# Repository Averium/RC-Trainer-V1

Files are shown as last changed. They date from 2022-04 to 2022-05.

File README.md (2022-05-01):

# RC-Trainer-V1

This project is a legal sized trainer RC aircraft design

# Specifications:

- Mass:         182 g
- Length:       520 mm
- Wingspawn:    708 mm
- CG:           157 mm

- Powerplant:   1 x 600 mah LIPO  -  1 x EMAX MT1806 2280 kv  -  5030 propeller (2 blade)
        
- 4 Channels:   Throttle - Elevator - Rudder - Ailerons

# Materials:
  - 5 mm foam board sheet
  - 3 mm plywood sheet
  - 4 mm BBQ stick
  - 12 x 12 mm balsa slat
  - 1 mm spring steel wire
  - 3D printed PLA plastic

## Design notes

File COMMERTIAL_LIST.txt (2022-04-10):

Motor		EMAX MT1806 2280kv
ESC		BHeli 12A		
Servo		3.7g micro
Propeller	5030 CF
Receiver	FS2A-4CH
Battery 	2s lipo 600 mah

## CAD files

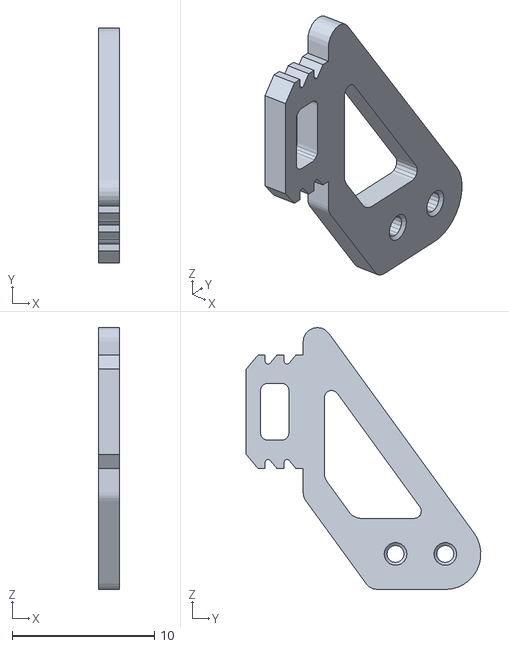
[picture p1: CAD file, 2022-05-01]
PARTS/PP-00-0-CONTROL_HORN/PP-00-0-0-M1.stl
1.50 x 16.5 x 18.4

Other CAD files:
PARTS/PP-00-0-CONTROL_HORN/PP-00-0-0-M2.stl
ASSEMBLY/A-00-0-MAIN/A-00-0.iam
ASSEMBLY/A-00-0-MAIN/A-00-0.idw
ASSEMBLY/A-01-0-FUSELAGE/A-01-0.iam
ASSEMBLY/A-01-0-FUSELAGE/A-01-0.idw
ASSEMBLY/A-01-0-FUSELAGE/A-01-0.ipn
ASSEMBLY/A-02-0-WING/A-02-0.iam
ASSEMBLY/A-02-0-WING/A-02-0.idw
ASSEMBLY/A-02-0-WING/A-02-0.ipn
ASSEMBLY/A-03-0-ONE_LEVEL/A-03-0.iam
PARTS/C-00-0-BATTERY_600MAH/C-00-0.ipt
PARTS/C-01-0-EMAX_MT1806_2280KV/C-01-0.ipt
PARTS/C-02-0-EMAX_12AESC/C-02-0.ipt
PARTS/C-03-0-SERVO_3G/C-03-0.ipt
PARTS/C-03-0-SERVO_3G/C-03-0/CCW.ipt
PARTS/C-03-0-SERVO_3G/C-03-0/CW.ipt
PARTS/C-04-0-SERVO_LINKAGE_STOPPER/C-04-0.ipt
PARTS/C-05-0-FS2A_4CH/C-05-0.ipt
PARTS/C-06-0-5030_PROPELLER/C-06-0.ipt
PARTS/PF-00-0-WING/PF-00-0-0.idw
PARTS/PF-00-0-WING/PF-00-0-0.ipt
PARTS/PF-00-0-WING/PF-00-0-1.ipt
PARTS/PF-01-0-FUSELAGE/PF-01-0-0.idw
PARTS/PF-01-0-FUSELAGE/PF-01-0-0.ipt
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

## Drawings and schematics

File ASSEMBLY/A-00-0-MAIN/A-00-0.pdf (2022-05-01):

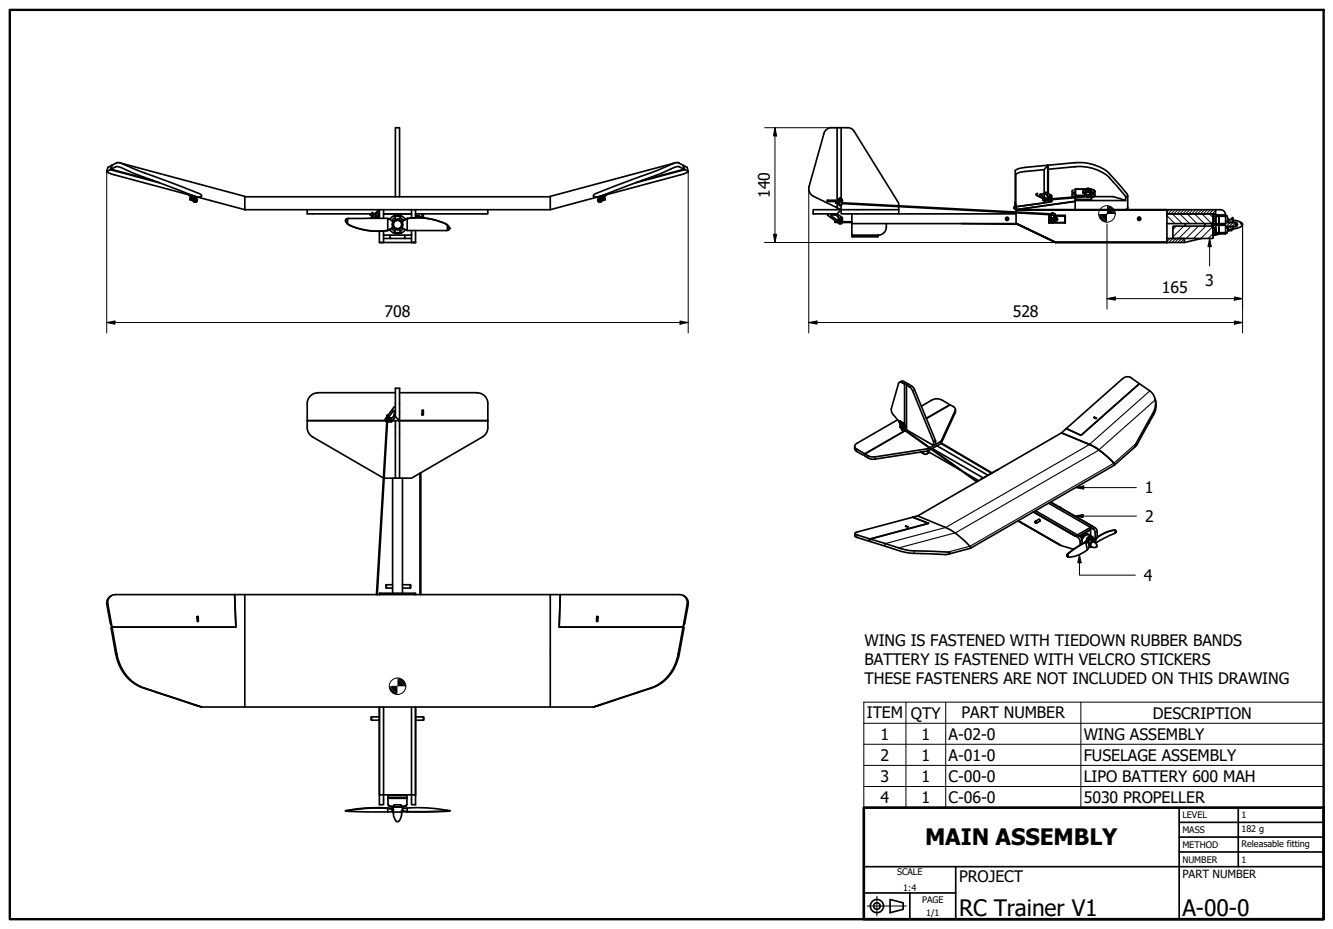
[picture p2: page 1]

WING IS FASTENED WITH TIEDOWN RUBBER BANDS
BATTERY IS FASTENED WITH VELCRO STICKERS
THESE FASTENERS ARE NOT INCLUDED ON THIS DRAWING

ITEM | QTY | PART NUMBER | DESCRIPTION
1 | 1 | A-02-0 | WING ASSEMBLY
2 | 1 | A-01-0 | FUSELAGE ASSEMBLY
3 | 1 | C-00-0 | LIPO BATTERY 600 MAH
4 | 1 | C-06-0 | 5030 PROPELLER
MAIN ASSEMBLY | LEVEL | 1

MASS | 182 g
METHOD | Releasable fitting
NUMBER | 1

SCALE 1:4 | PROJECT RC Trainer V1 | PART NUMBER A-00-0

PAGE 1/1

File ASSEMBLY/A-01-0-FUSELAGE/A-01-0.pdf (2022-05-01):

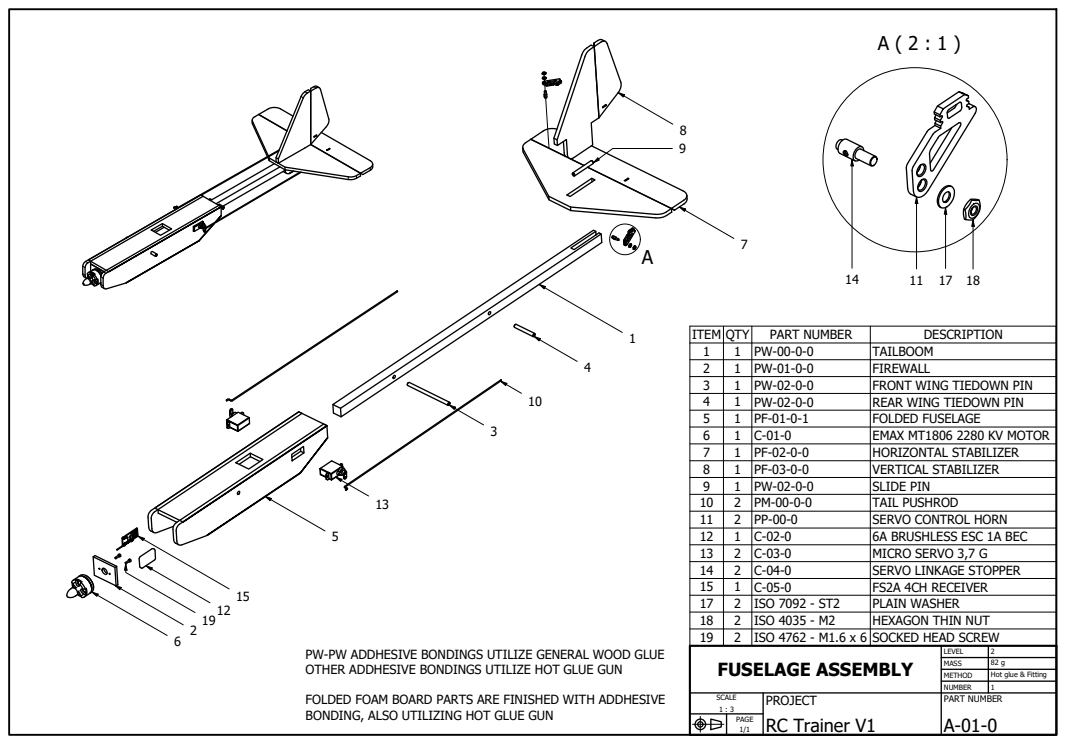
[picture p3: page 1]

ITEM | QTY | PART NUMBER | DESCRIPTION
1 | 1 | PW-00-0-0 | TAILBOOM
2 | 1 | PW-01-0-0 | FIREWALL
3 | 1 | PW-02-0-0 | FRONT WING TIEDOWN PIN
4 | 1 | PW-02-0-0 | REAR WING TIEDOWN PIN
5 | 1 | PF-01-0-1 | FOLDED FUSELAGE
6 | 1 | C-01-0 | EMAX MT1806 2280 KV MOTOR
7 | 1 | PF-02-0-0 | HORIZONTAL STABILIZER
8 | 1 | PF-03-0-0 | VERTICAL STABILIZER
9 | 1 | PW-02-0-0 | SLIDE PIN
10 | 2 | PM-00-0-0 | TAIL PUSHROD
11 | 2 | PP-00-0 | SERVO CONTROL HORN
12 | 1 | C-02-0 | 6A BRUSHLESS ESC 1A BEC
13 | 2 | C-03-0 | MICRO SERVO 3,7 G
14 | 2 | C-04-0 | SERVO LINKAGE STOPPER
15 | 1 | C-05-0 | FS2A 4CH RECEIVER
17 | 2 | ISO 7092 - ST2 | PLAIN WASHER
18 | 2 | ISO 4035 - M2 | HEXAGON THIN NUT
19 | 2 | ISO 4762 - M1.6 x 6 | SOCKED HEAD SCREW
FUSELAGE ASSEMBLY | LEVEL | 2

PW-PW ADDHESIVE BONDINGS UTILIZE GENERAL WOOD GLUE
OTHER ADDHESIVE BONDINGS UTILIZE HOT GLUE GUN

MASS | 82 g
METHOD | Hot glue & Fitting
NUMBER | 1

FOLDED FOAM BOARD PARTS ARE FINISHED WITH ADDHESIVE
BONDING, ALSO UTILIZING HOT GLUE GUN

SCALE 1 : 3 | PROJECT RC Trainer V1 | PART NUMBER A-01-0

PAGE 1/1

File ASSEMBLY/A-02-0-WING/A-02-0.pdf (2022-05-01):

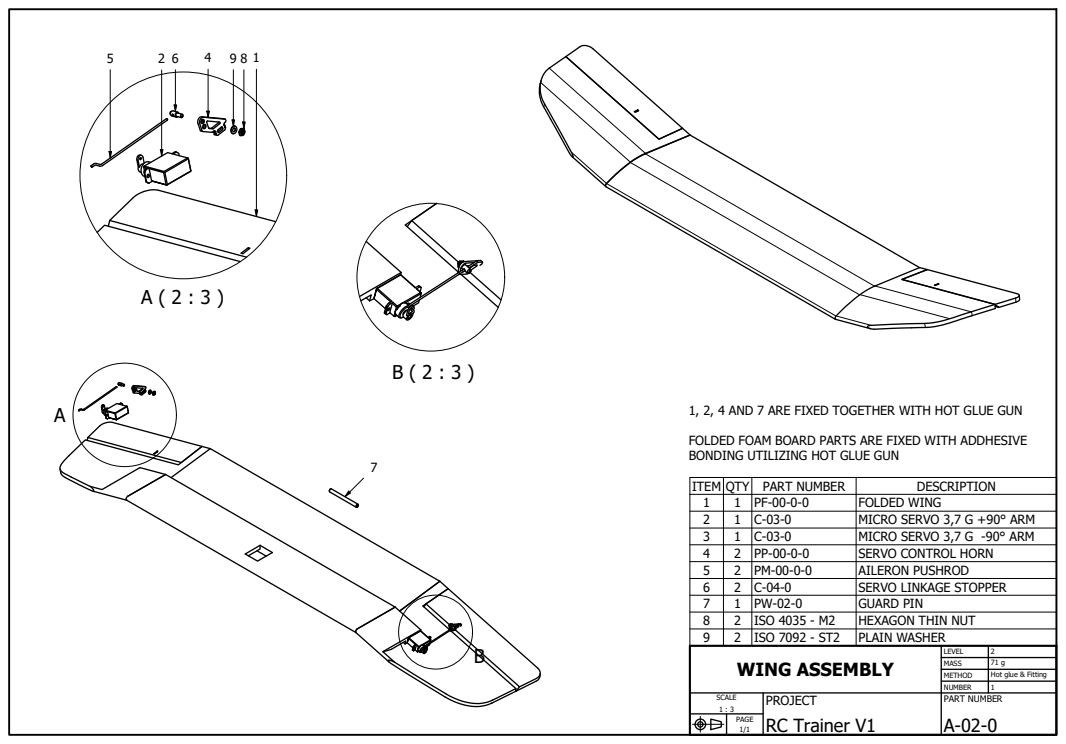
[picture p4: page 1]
WING ASSEMBLY

1, 2, 4 AND 7 ARE FIXED TOGETHER WITH HOT GLUE GUN

FOLDED FOAM BOARD PARTS ARE FIXED WITH ADDHESIVE
BONDING UTILIZING HOT GLUE GUN

ITEM | QTY | PART NUMBER | DESCRIPTION
1 | 1 | PF-00-0-0 | FOLDED WING
2 | 1 | C-03-0 | MICRO SERVO 3,7 G +90° ARM
3 | 1 | C-03-0 | MICRO SERVO 3,7 G -90° ARM
4 | 2 | PP-00-0-0 | SERVO CONTROL HORN
5 | 2 | PM-00-0-0 | AILERON PUSHROD
6 | 2 | C-04-0 | SERVO LINKAGE STOPPER
7 | 1 | PW-02-0 | GUARD PIN
8 | 2 | ISO 4035 - M2 | HEXAGON THIN NUT
9 | 2 | ISO 7092 - ST2 | PLAIN WASHER

LEVEL | 2
MASS | 71 g
METHOD | Hot glue & Fitting
NUMBER | 1

SCALE 1 : 3 | PROJECT RC Trainer V1 | PART NUMBER A-02-0

PAGE 1/1

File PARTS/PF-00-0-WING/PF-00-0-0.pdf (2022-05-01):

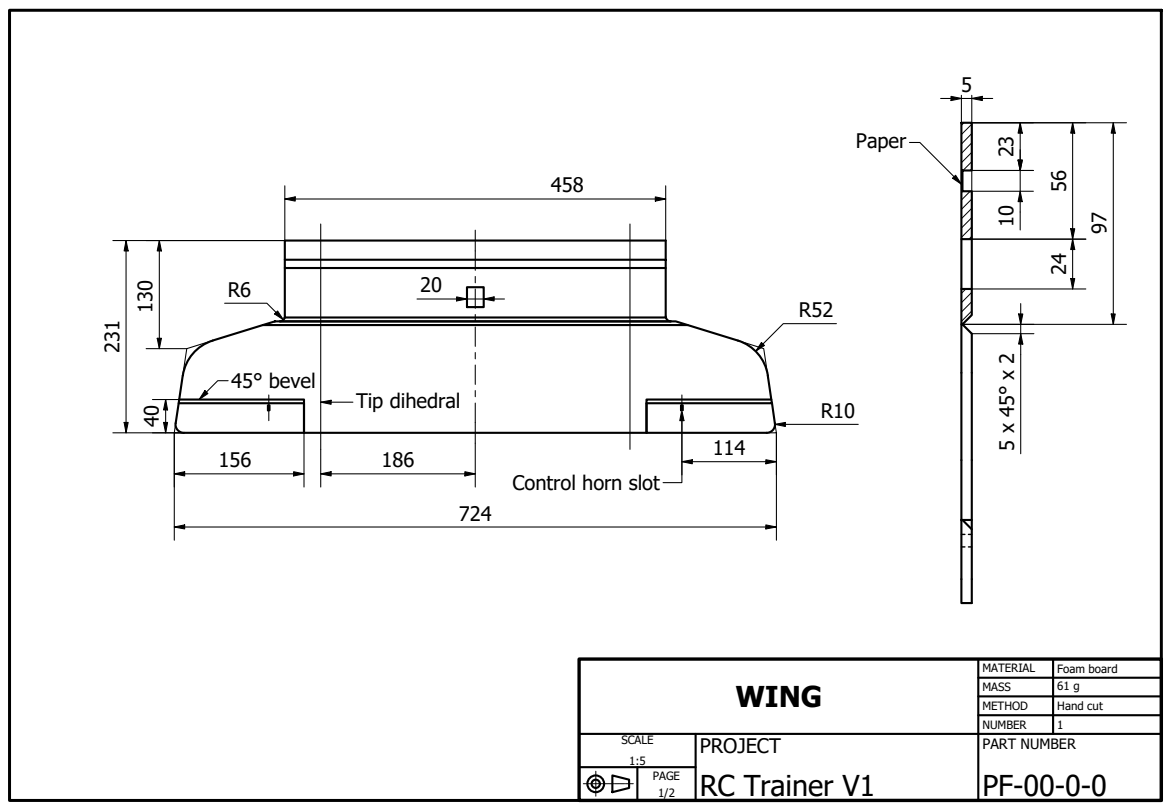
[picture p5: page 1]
Tip dihedral; 45° bevel

Control horn slot

WING | MATERIAL | Foam board

MASS | 61 g
METHOD | Hand cut
NUMBER | 1

SCALE 1:5 | PROJECT RC Trainer V1 | PART NUMBER PF-00-0-0

PAGE 1/2

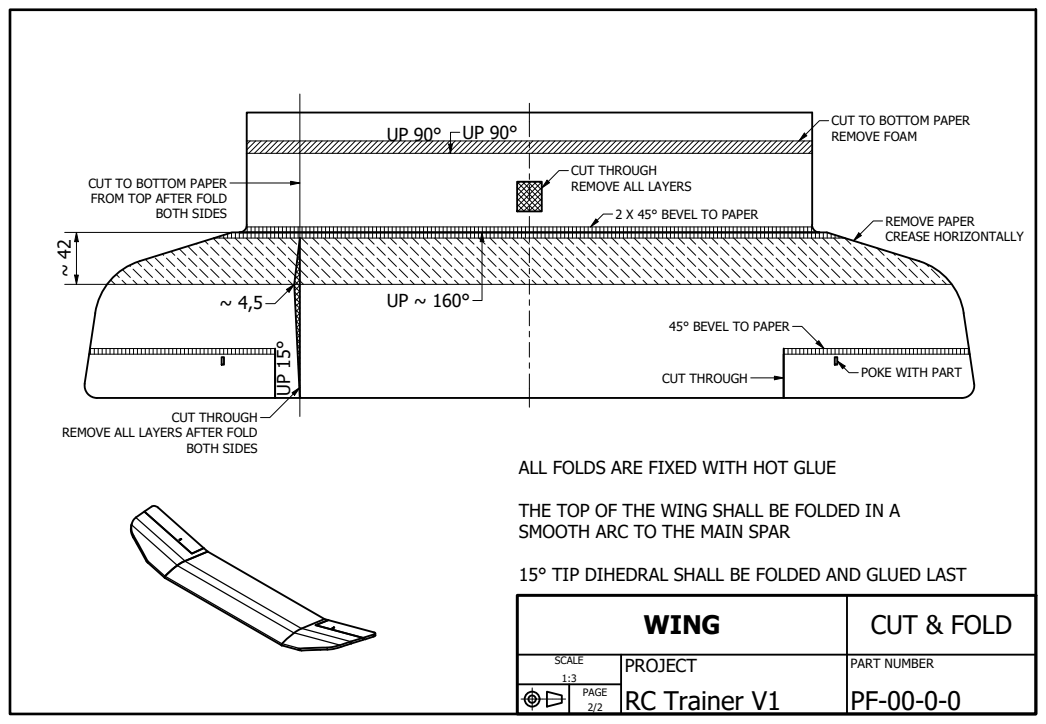
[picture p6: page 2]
REMOVE PAPER CREASE HORIZONTALLY; BOTH SIDES; CUT THROUGH

CUT TO BOTTOM PAPER
REMOVE FOAM

CUT THROUGH
REMOVE ALL LAYERS

FROM TOP AFTER FOLD

2 X 45° BEVEL TO PAPER

45° BEVEL TO PAPER

POKE WITH PART

REMOVE ALL LAYERS AFTER FOLD

ALL FOLDS ARE FIXED WITH HOT GLUE

THE TOP OF THE WING SHALL BE FOLDED IN A
SMOOTH ARC TO THE MAIN SPAR

15° TIP DIHEDRAL SHALL BE FOLDED AND GLUED LAST

WING | CUT & FOLD

SCALE 1:3 | PROJECT RC Trainer V1 | PART NUMBER PF-00-0-0

PAGE 2/2

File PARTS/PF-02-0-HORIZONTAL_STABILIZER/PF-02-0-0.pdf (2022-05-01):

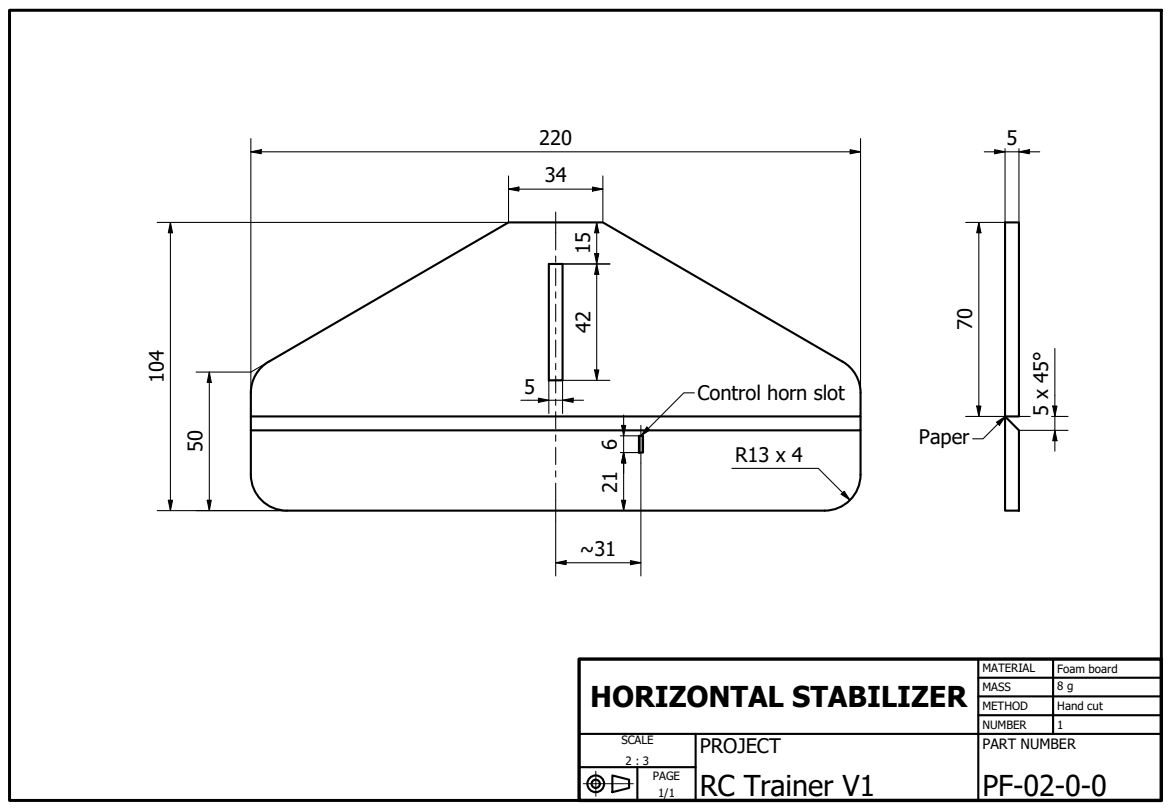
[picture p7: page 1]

Control horn slot

HORIZONTAL STABILIZER | MATERIAL | Foam board

MASS | 8 g
METHOD | Hand cut
NUMBER | 1

SCALE 2 : 3 | PROJECT RC Trainer V1 | PART NUMBER PF-02-0-0

PAGE 1/1

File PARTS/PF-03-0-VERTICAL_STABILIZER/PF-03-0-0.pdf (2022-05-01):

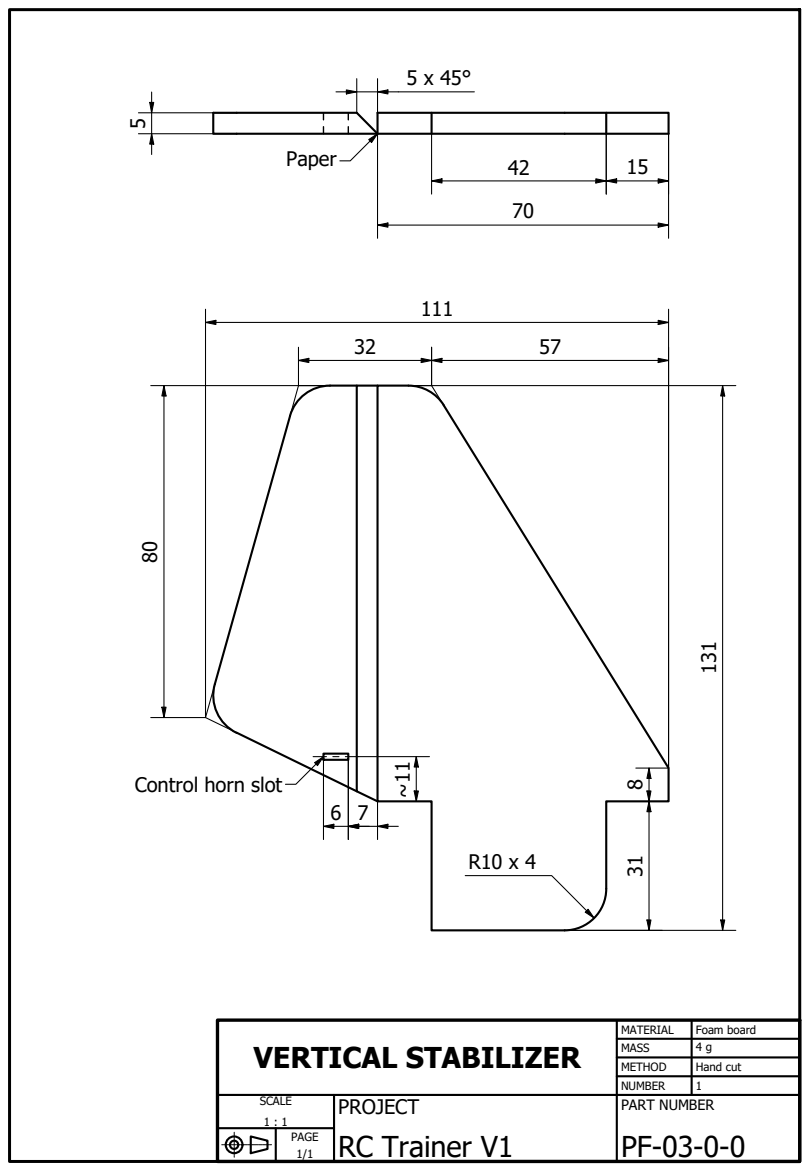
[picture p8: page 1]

Control horn slot

VERTICAL STABILIZER | MATERIAL | Foam board

MASS | 4 g
METHOD | Hand cut
NUMBER | 1

SCALE 1 : 1 | PROJECT RC Trainer V1 | PART NUMBER PF-03-0-0

PAGE 1/1

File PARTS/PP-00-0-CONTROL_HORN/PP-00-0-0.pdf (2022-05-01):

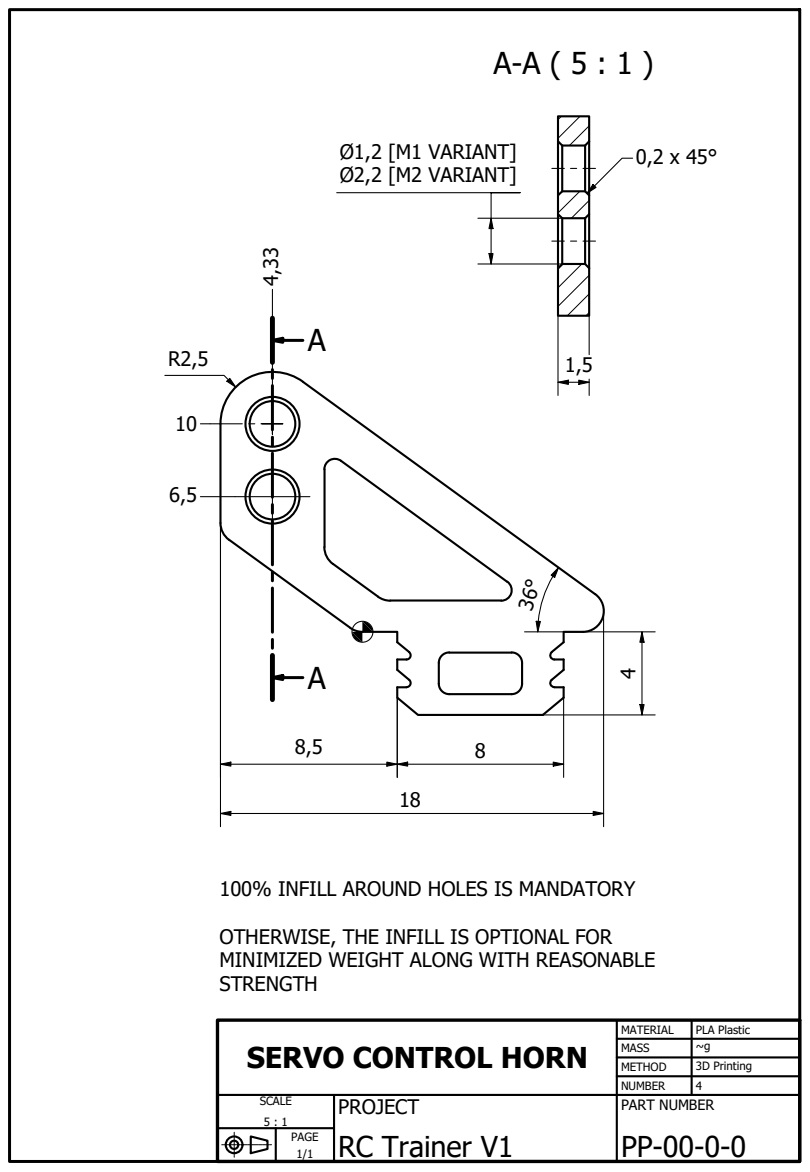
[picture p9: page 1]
Ø1,2 [M1 VARIANT] Ø2,2 [M2 VARIANT]

100% INFILL AROUND HOLES IS MANDATORY

OTHERWISE, THE INFILL IS OPTIONAL FOR
MINIMIZED WEIGHT ALONG WITH REASONABLE
STRENGTH

SERVO CONTROL HORN | MATERIAL | PLA Plastic

MASS | ~g
METHOD | 3D Printing
NUMBER | 4

SCALE 5 : 1 | PROJECT RC Trainer V1 | PART NUMBER PP-00-0-0

PAGE 1/1

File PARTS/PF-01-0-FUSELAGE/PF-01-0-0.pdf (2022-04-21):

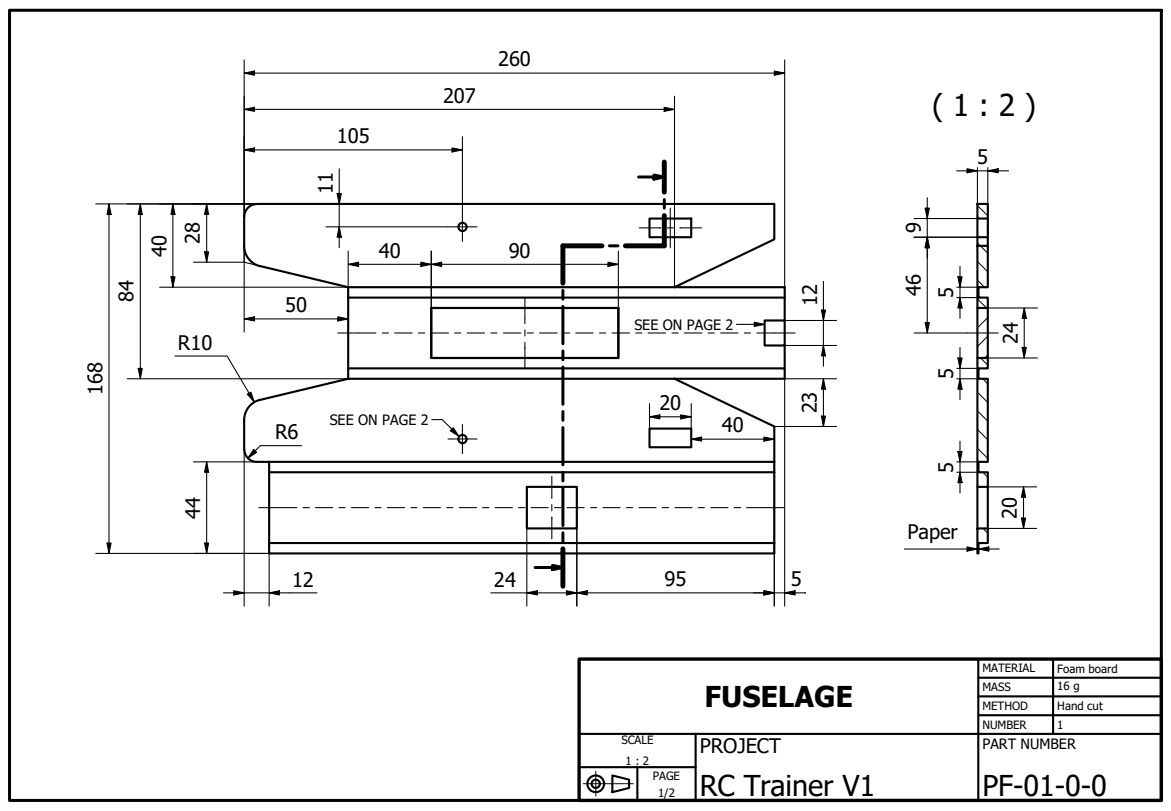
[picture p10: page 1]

SEE ON PAGE 2

FUSELAGE | MATERIAL | Foam board

MASS | 16 g
METHOD | Hand cut
NUMBER | 1

SCALE 1 : 2 | PROJECT RC Trainer V1 | PART NUMBER PF-01-0-0

PAGE 1/2

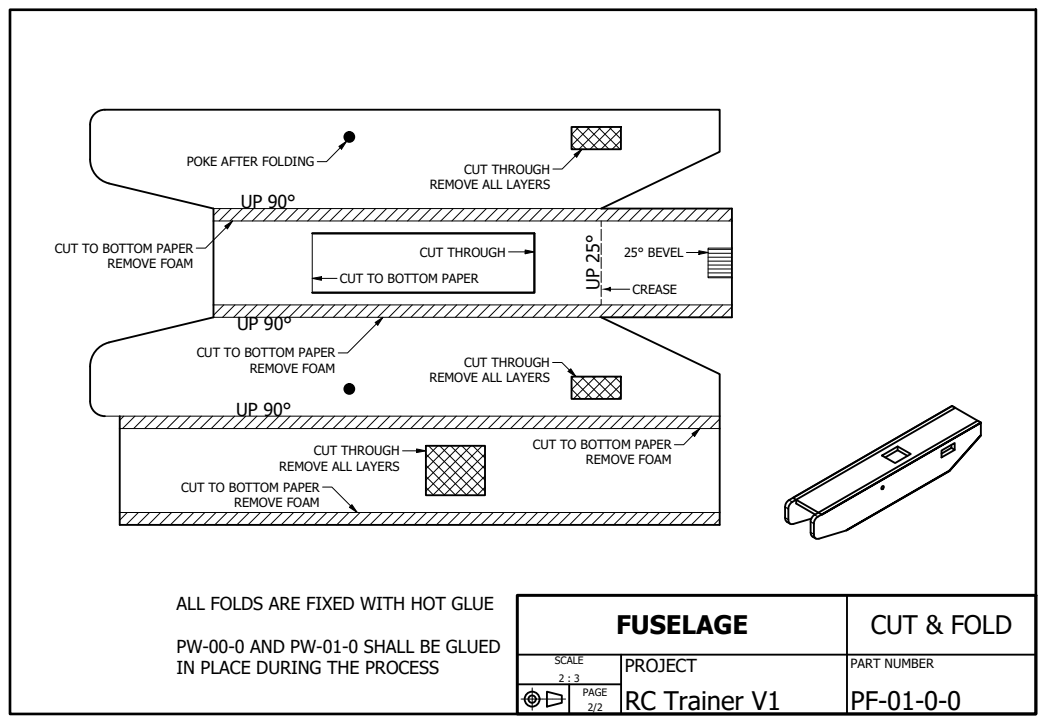
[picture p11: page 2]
REMOVE FOAM; CUT THROUGH; 25° BEVEL

POKE AFTER FOLDING

CUT THROUGH
REMOVE ALL LAYERS

CUT TO BOTTOM PAPER

ALL FOLDS ARE FIXED WITH HOT GLUE

FUSELAGE | CUT & FOLD

PW-00-0 AND PW-01-0 SHALL BE GLUED
IN PLACE DURING THE PROCESS

SCALE 2 : 3 | PROJECT RC Trainer V1 | PART NUMBER PF-01-0-0

PAGE 2/2

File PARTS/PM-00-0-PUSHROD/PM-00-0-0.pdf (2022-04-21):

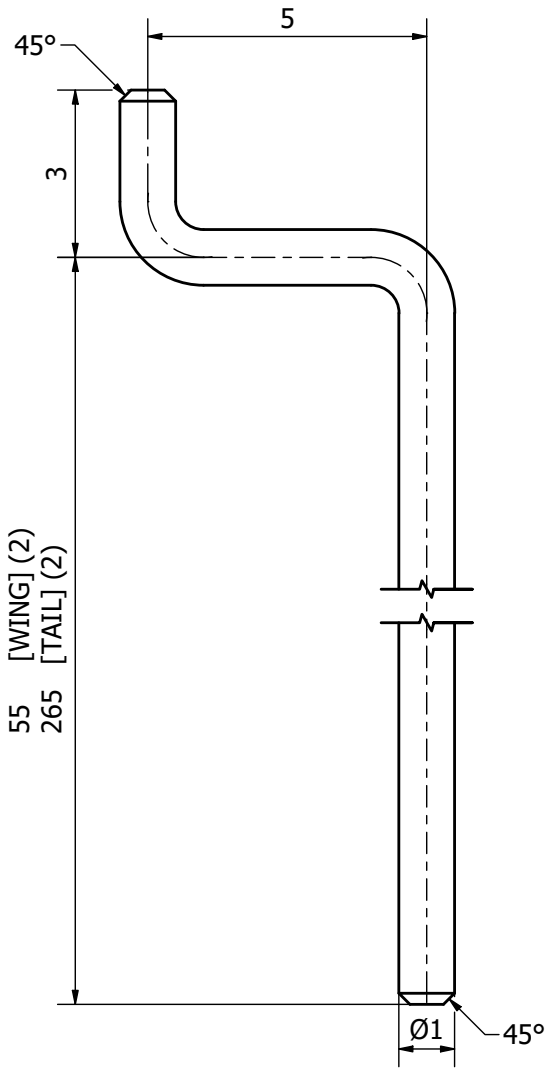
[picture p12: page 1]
5 [WIN; 5 [TAIL] (2)

PUSHROD | MATERIAL | Spring steel wire

MASS | ~g
METHOD | Hand cut & Bend
NUMBER | 4

SCALE 10 : 1 | PROJECT RC Trainer V1 | PART NUMBER PM-00-0-0

PAGE 1/1

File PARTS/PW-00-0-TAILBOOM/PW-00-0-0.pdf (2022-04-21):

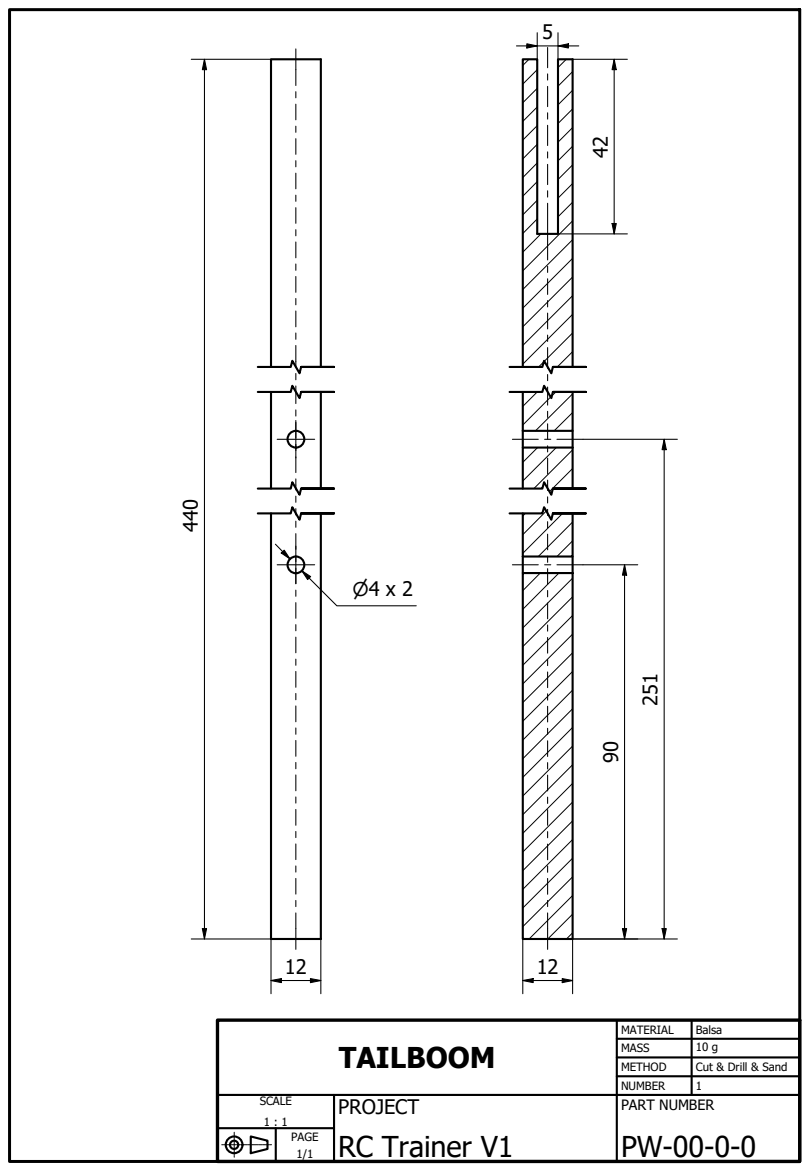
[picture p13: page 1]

TAILBOOM | MATERIAL | Balsa

MASS | 10 g
METHOD | Cut & Drill & Sand
NUMBER | 1

SCALE 1 : 1 | PROJECT RC Trainer V1 | PART NUMBER PW-00-0-0

PAGE 1/1

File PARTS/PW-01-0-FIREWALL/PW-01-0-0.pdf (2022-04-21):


FIREWALL | MATERIAL | Plywood

MASS | 2 g
METHOD | Cut & Drill & Sand
NUMBER | 1

SCALE 3 : 1 | PROJECT RC Trainer V1 | PART NUMBER PW-01-0-0

PAGE 1/1

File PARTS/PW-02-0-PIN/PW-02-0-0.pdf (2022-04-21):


STICK PIN | MATERIAL | Wooden stick

MASS | ~g
METHOD | Hand cut & Sand
NUMBER | 3

SCALE 5 : 1 | PROJECT RC Trainer V1 | PART NUMBER PW-02-0-0

PAGE 1/1

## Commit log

2022-04-10 Updated file structure
    [A-00-0.0036.iam, A-00-0.0036.idw, A-00-0.iam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]
2022-04-15 Fixed missing dimensions
    [PF-00-0-0.0019.ipt, PF-00-0-0.0036.idw, PF-00-0-0.idw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]
2022-04-18 cut and fold patterns for foam parts
    [A-00-0.0039.iam, A-00-0.0043.idw, A-00-0.iam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]
2022-04-18 Added missing pdf files
    [PF-00-0-0.0058.idw, PF-00-0-0.0059.idw, PF-00-0-0.idw]
2022-04-18 Removed old version files
    [A-00-0.0039.iam, A-00-0.0043.idw, A-00-0.iam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]
2022-04-21 Minor modifications
    Fixed and improved some parts while building the model in real life.
    [A-00-0.iam, A-00-0.idw, A-01-0.iam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]
2022-05-01 Redesigned servo control horns
    [A-00-0.iam, A-00-0.idw, A-01-0.iam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]
